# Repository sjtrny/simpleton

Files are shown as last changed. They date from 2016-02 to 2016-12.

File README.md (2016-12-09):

# simpleton

The Simpleton flight controller.
[NO LONGER UNDER DEVELOPMENT]

Features of Simpleton:

* STM32F3 MCU
* Power distribution for your ESCs and accessories
* On board OSD, configurable in cleanflight configurator
* MPU-6000 (via SPI)
* Powered directly from flight battery (up to 6S)
* Current monitoring
* Selectable 12V or 9V power for HS1177 and VTX
* 4x ESC out
* 3x UARTs (invertible) for serial receivers and accesories
* 256Mb flash storage
* Buzzer Out

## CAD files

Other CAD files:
layout/original/simpleton_layout_1.skp
layout/original/simpleton_layout_2.skp
layout/original/simpleton_layout_2~.skp

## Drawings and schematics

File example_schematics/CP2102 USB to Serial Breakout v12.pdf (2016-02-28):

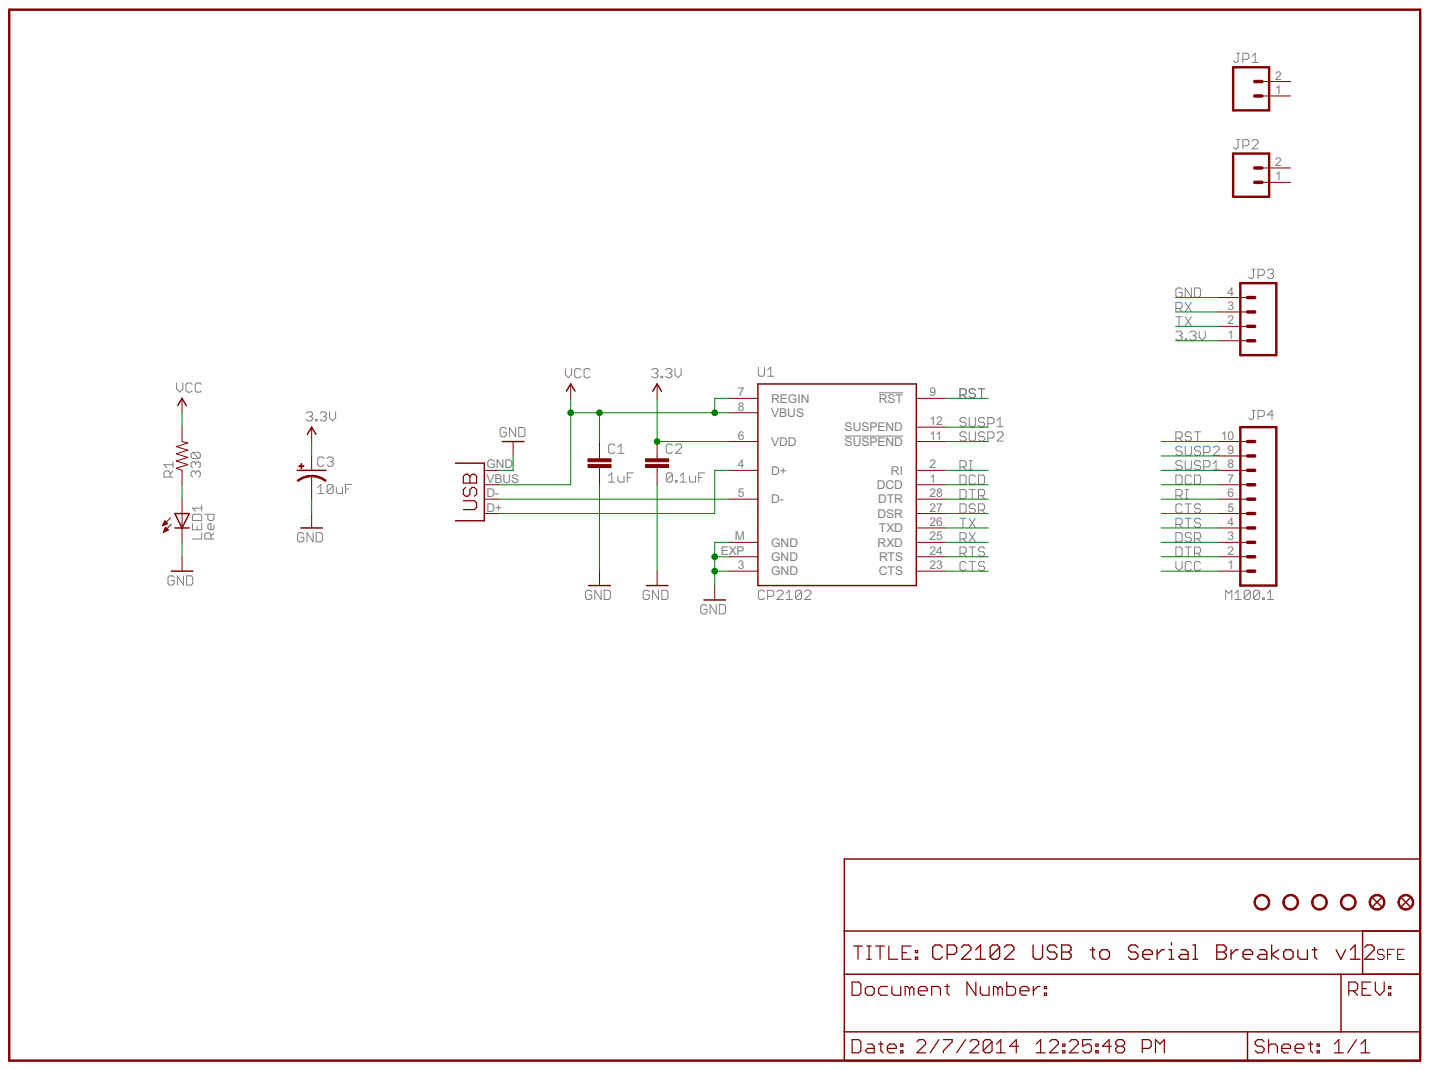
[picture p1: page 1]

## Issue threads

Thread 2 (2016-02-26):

Add MCU power supply circuitry

sjtrny, 2016-02-26:
We need the following:
- 3.3V regulator
- 5.5V regulator
- Route power from USB
- Route from flight battery
- Safe operation when both USB and flight battery are connected
- MCU power supply decoupling

Tasks:
- Create 3.3V regulator component
- Create 5V regulator component
- Create USB jack component
- Route from USB/flight battery pads through ORing diode funnel to 3.3V regulator
- Add MCU decoupling caps and associated routing

sjtrny, 2016-02-27:
3.3V regulator: RT9193-33GB
5V regulator: MP1584 (same as used in DSUN, will also use it for 12V to make things easier and cheaper)

sjtrny, 2016-02-27:
For the MCU we need the following:

- 1x 100nF bypass caps for each VDD
- 1x 4.7uF bypass cap for one of the VDD pins
- 1x 2.2uF cap between VCAP_1 and GND
- 1x 2.2uF cap between VCAP_2 and GND
- 1x 100nF bypass cap for VDDA
- 1x 1uF bypass cap for VDDA
- Connect all VSS to GND

Closed 2016-02-27.

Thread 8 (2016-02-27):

Add UARTs and inverters

sjtrny, 2016-02-27:
Use XOR gates as controlled inverters for all UART TX and RX.

sjtrny, 2016-02-29:
We will use 3x SN74LVC2G86 from TI, one for each accessible UART.

sjtrny, 2016-02-29:
While we are here we should add 3.3V out pin for spek sats

Closed 2016-02-29.

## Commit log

2016-02-26 Initial commit
    Blank kicad project etc
    [simpleton.kicad_pcb, simpleton.sch]
2016-02-26 Created STM32F405RG component
    Closes #1
    [simpleton.sch]
2016-02-27 Added MCU power supply circuitry
    Closes #2
    [simpleton.sch]
2016-02-28 Added CP2104
    Closes #3
    - Created CP2104 part
    - Added CP2104 to schematic and wired to USB power and USART1
    - Added datasheet
    [simpleton.sch]
2016-02-28 Added MPU6000
    Closes #5
    - Added MPU6000 data sheet
    - Created MPU6000 component
    - Connected MPU6000 to power and SPI_1
    [simpleton.sch]
2016-02-28 Connected MPU interrupt pin to MCU
    [simpleton.sch]
2016-02-29 Added flash storage
    Closes #6
    - Added data sheet
    - Created N25Q256A33EF840 part
    - Connected N25Q256A to power and SPI
    [simpleton.sch]
2016-02-29 Added MAX7456
    Closes #7
    - Created MAX7456 component
    - Connected component to SPI3 and power
    [simpleton.sch]
2016-02-29 Added UARTs and inverters
    Closes #8
    - Added SN74LVC2G86 data sheet
    - Created SN74LVC2G86 component
    - Wired up 3x SN74LVC2G86 (one for each UART) in the schematic
    [simpleton.sch]
2016-02-29 Added vid ports and spek sat power port
    Closes #13
    [simpleton.sch]
2016-02-29 Added ESC outputs
    Closes #9
    [simpleton.sch]
2016-03-01 Added 9/12V regulator
    Closes #10
    - Added regulator for 9/12V
    - Added jumper for for voltage selection
    [simpleton.sch]
2016-03-01 Added voltage divider
    Closes #12
    - R1 = 70k, R2 = 10k
    - Supports HV 6S operation
    [simpleton.sch]
2016-03-01 Added buzzer
    Closes #11
    [simpleton.sch]
2016-03-01 Added status LEDS
    Closes #4
    [simpleton.sch]
2016-04-17 Added boot loader support
    Closes #14
    [simpleton.sch]
2016-06-06 Added Sketchup layout files
    [simpleton_layout_1.skp, simpleton_layout_2.skp, simpleton_layout_2~.skp]
2016-06-07 Moved to STM32F3 solution
    - Swapped MCU
    - Added current sensor
    - Increase 3.3V regulator to 500mA version
    - Removed UART inverters
    [simpleton.sch]
